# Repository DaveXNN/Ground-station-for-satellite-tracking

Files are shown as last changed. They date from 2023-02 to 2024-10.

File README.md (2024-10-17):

# Ground station for satellite tracking
This repository contains a description of the project Ground station for satellite tracking. The goal of this project was to build a ground satellite station that is able to receive signals from satellites operating at VHF (Very High Frequency) and UHF (Ultra High Frequency). The ground station constists of rotator, antennas, polarization switcher, receiver and station computer (laptop). Each part is describet in separate chapter.

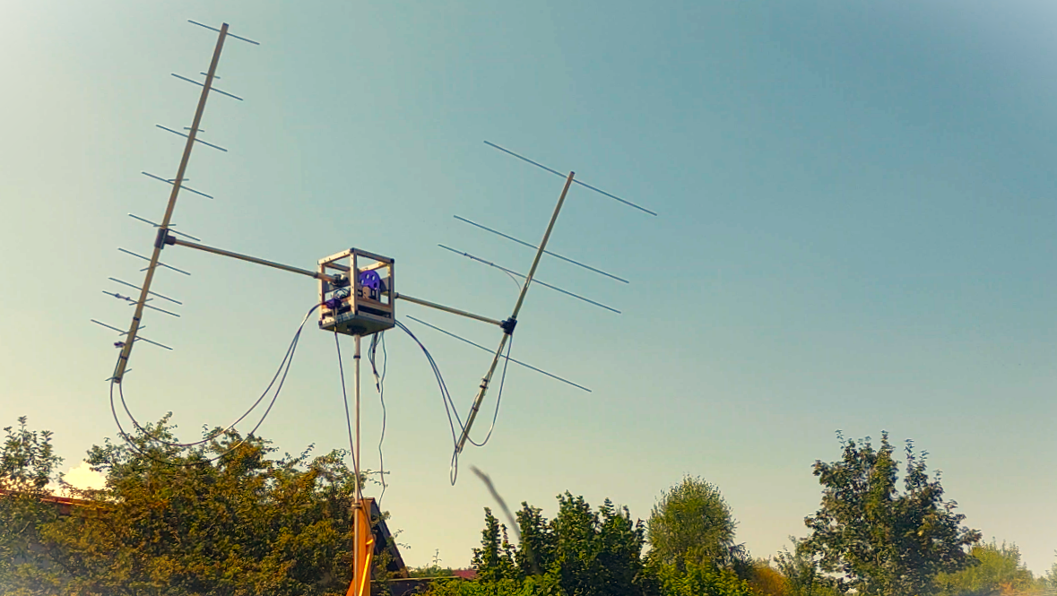
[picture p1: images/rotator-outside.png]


## Rotator
Unfortunately, a lot of these satellites are situated on the LEO (Low Earth Orbit), in other words below the altitude of 2 000 km. It means that the satellite changes its position very quickly and it's very uncomfortable to change antennas' direction manually, because it may cause a loss of the satellite signal. A rotator is a good solution of this problem, because this device moves the antennas automatically with very high precision.

### Design
Of course there are many proffesional rotators available to buy in the internet e.g. Yaesu, but i decided to build a similar rotator by myself, because it's cheaper option and I really wanted to get into this field of problems. I've got an inspiration from [SatNOGS Rotator v3](https://wiki.satnogs.org/SatNOGS_Rotator_v3).

The rotator frame is made from aluminium and wood and has dimensions of 240x240x305 mm. There are also 4 bearings installed, 2 to hold azimuth rod and 2 to hold elevation rod. It's also designed to mantle and dismantle easily, so each of the rods can be installed or removed quickly. Spur gears are used to make the rods to move. They are available with all 3D-printed parts in [this repository](/stl-files/rotator).

### Electronic components

The device is supplied by 45 W laptop charger providing 20 V voltage. This voltage is used to supply stepper motors, but it's also reduced into 5 V using step-down voltage regulator to supply control unit and polarization switchers. The control unit of the rotator is computer [Raspberry Pi 4](https://www.raspberrypi.com/products/raspberry-pi-4-model-b/) with its digital GPIO pins. Raspberry Pi controls two stepper motor drivers TB6600 and two polarization switchers described in chapter 3. The device is designed to require as few cables as possible so the communication between the rotator and station computer runs through WiFi.

Here is a list of electronic components:

| Name  | Quantity | Link |
| :--- | :---: | :---: |
| Raspberry Pi 4B  | 1  | https://www.raspberrypi.com/products/raspberry-pi-4-model-b/ |
| Step-Down Voltage Regulator LM2596 | 1 | https://www.laskakit.cz/step-down-menic-s-lm2596/ |
| Stepper motor NEMA23  | 2 | https://www.laskakit.cz/krokovy-motor-nema-23-57hs5630a4d8-1-1nm/ |
| Driver TB6600  | 2 | https://www.laskakit.cz/driver-tb6600--tb67s109aftg--pro-krokove-motory-3a-47v/ |
| Laptop charger 45 W | 1  |  |

#### Raspberry Pi 4B
The next picture depicts Raspberry Pi 4B pinout:

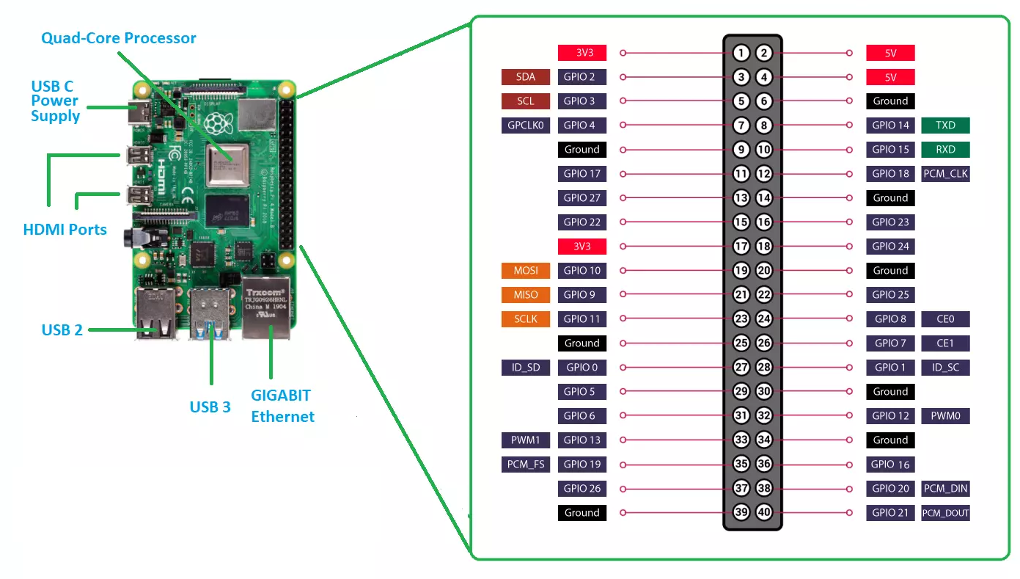
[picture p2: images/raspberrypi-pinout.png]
Raspberry Pi 4 pinout (www.theengineeringprojects.com)


In the next table you can see Raspberry Pi digital pins and their usage:

| Name | Pin number | GPIO code | Connected device | Description |
| :--- | :---: | :---: | :---: | :---: |
| VCC | 17 | 3V3 | Azimuth/elevation stepper motor driver | provides 3.3 V for controling drivers |
| az.ENA | 19 | GPIO10 | Azimuth stepper motor driver | enables stepper motor to move |
| az.DIR | 21 | GPIO9 | Azimuth stepper motor driver | sets rotation direction |
| az.PUL | 23 | GPIO11 | Azimuth stepper motor driver | used to do 1 single step |
| el.ENA | 11 | GPIO17 | Elevation stepper motor driver | enables stepper motor to move |
| el.DIR | 13 | GPIO27 | Elevation stepper motor driver | sets rotation direction |
| el.PUL | 15 | GPIO22 | Elevation stepper motor driver | used to do 1 single step |
| pol_sw.UHF_REL1 | 27 | GPIO0 | UHF polarization switcher | controls relay 1 |
| pol_sw.UHF_REL2 | 29 | GPIO5 | UHF polarization switcher | controls relay 2 |
| pol_sw.VHF_REL1 | 31 | GPIO6 | VHF polarization switcher | controls relay 1 |
| pol_sw.VHF_REL2 | 33 | GPIO13 | VHF polarization switcher | controls relay 2 |

#### Driver TB6600 (2x)
Driver TB6600 is supposed to control a stepper motor with a power supply 20 V. It has three inputs for controling stepper motor - ENA (enable), DIR (direction) and PUL (pulse) and for outputs A+, A-, B+, B-. Here is a list of all inputs and outputs of one stepper motor driver:

| Name | I/O | Connected device| Cable color | Voltage |
| :--- | :---: | :---: | :---: | :---: |
| ENA- | input | Raspberry Pi | green | 0/3.3 V |
| ENA+ | input | Raspberry Pi | red | 3.3 V |
| DIR- | input | Raspberry Pi | yellow | 0/3.3 V |
| DIR+ | input | Raspberry Pi | red | 3.3 V |
| PUL- | input | Raspberry Pi | orange | 0/3.3 V |
| PUL+ | input | Raspberry Pi | red | 3.3 V |
| B- | output | stepper motor | black | 0-20 V |
| B+ | output | stepper motor | green | 0-20 V |
| A- | output | stepper motor | blue | 0-20 V |
| A+ | output | stepper motor | red | 0-20 V |
| GND | input | Laptop charger | black | 0 V |
| VCC | input | Laptop charger | white | 20 V |

Each of the drivers also has six switches to set up peak current and microstep. Peak current is set to 0,7 V and microstep to level 4, it means that the position of the switches is: S1-ON, S2-OFF, S3-OFF, S4-ON, S5-ON, S6-ON.

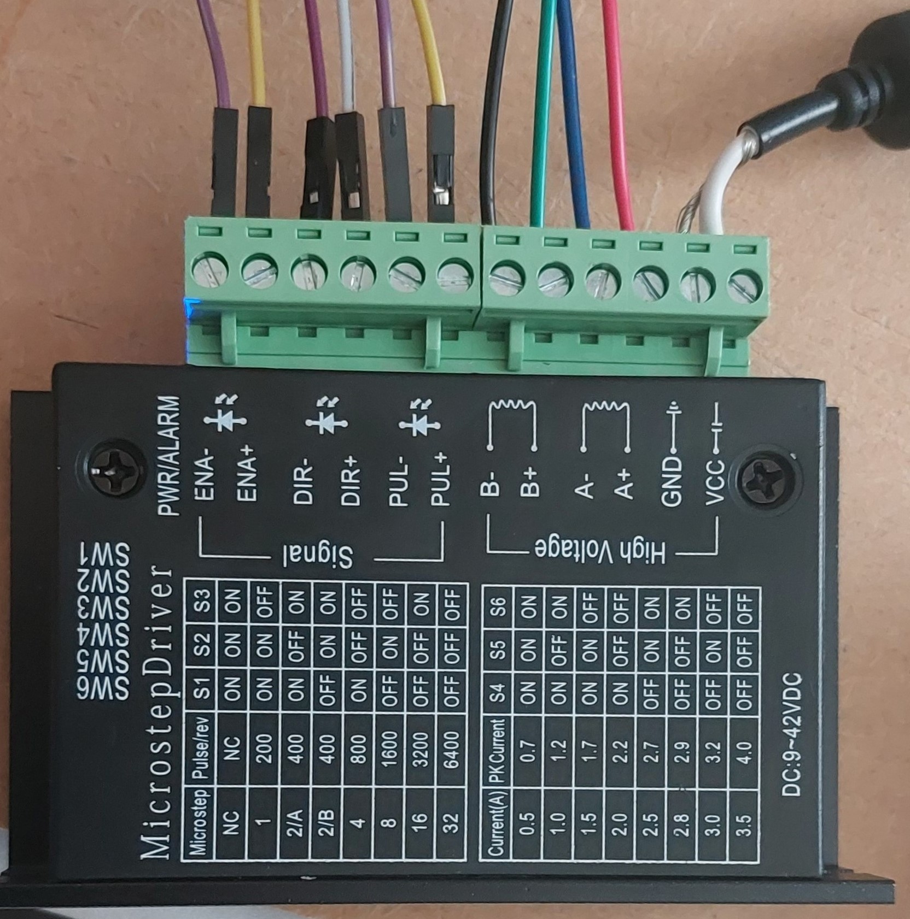
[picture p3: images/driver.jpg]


#### Stepper motor NEMA23 (2x)
NEMA23 is a high torque stepper motor with torque over 1,8 Nm and step angle 1,8°. It's connected with 4 wires (black, green, blue, red) to the driver. Stepper motors move the rotator via spur gears. In the next picture you can see spur gears for azimuth and elevation control.

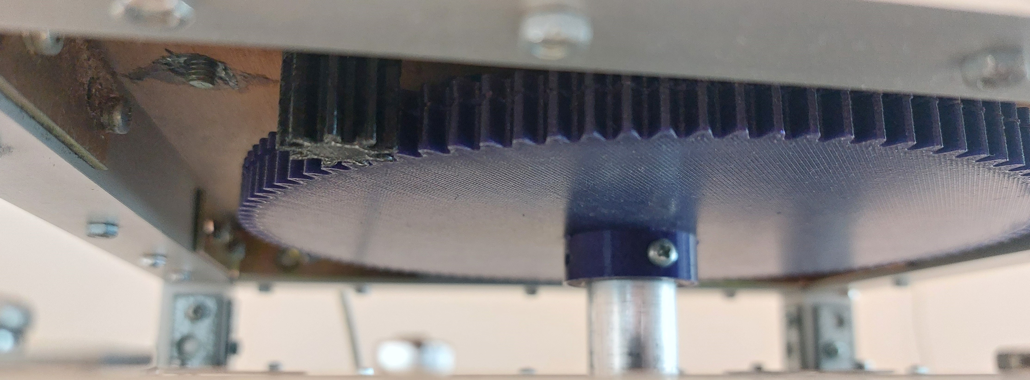
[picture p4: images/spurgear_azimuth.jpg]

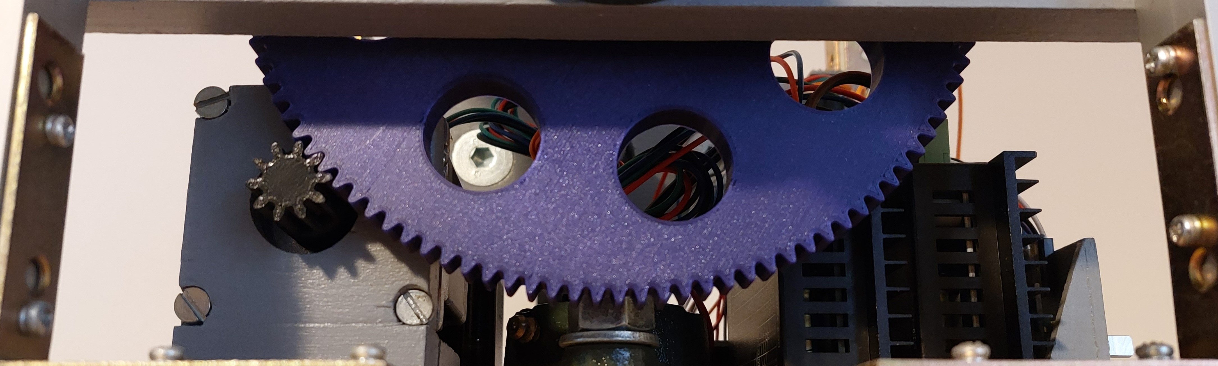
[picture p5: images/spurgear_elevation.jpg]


### Rotator software
Rotator receives commands via MQTT client and then moves stepper motors or changes antenna polarization. It's programmed in Python 3.9 and you can find the source code in [this repository](/source_code/rotator).

To install MQTT broker on Raspberry Pi I used a command ```sudo apt install -y mosquitto mosquitto-clients```

and to make Mosquitto auto start when the Raspberry Pi boots I used a command ```sudo systemctl enable mosquitto.service```.

[Rotator.py](/source_code/rotator/Rotator.py) is a main script that is run on boot. It initializes all modules and subscribes topics used to control rotator. There is also module [Stepper.py](/source_code/rotator/Stepper.py) to control stepper motors, module [PolarizationSwitcher.py](/source_code/rotator/PolarizationSwitcher.py) to control polarazation switchers and module [Publisher.py](/source_code/rotator/Publisher.py) to send rotator current azimuth and elevation back to station computer.

Here is a list of used Python packages:
* [RPi.GPIO](https://pypi.org/project/RPi.GPIO/) - controling digital pins
* [paho-mqtt](https://pypi.org/project/paho-mqtt/) - communicating with MQTT broker
* [threading](https://docs.python.org/3/library/threading.html) - running functions in parallel
* [time](https://docs.python.org/3/library/time.html) - time acces and conversions

For running script on boot of Raspberry Pi, I modified file ```/etc/rc.local``` by adding a line ```python3 /home/rotator/Rotator.py```, so the final file looks like this:
```
#!/bin/sh -e
#
# rc.local
#
# This script is executed at the end of each multiuser runlevel.
# Make sure that the script will "exit 0" on success or any other
# value on error.
#
# In order to enable or disable this script just change the execution
# bits.
#
# By default this script does nothing.

# Print the IP address
_IP=$(hostname -I) || true
if [ "$_IP" ]; then
  printf "My IP address is %s\n" "$_IP"
fi

python3 /home/rotator/Rotator.py &

exit 0
```

## Yagi antennas
The rotator has two arms equiped with cross-Yagi antennas for VHF and UHF. The VHF Yagi antenna is designed for frequency 145 MHz and the UHF Yagi antenna is designed for 435 MHz. The antennas are made from aluminium. For boom is made from 20 mm square rod and the elements are made from 6 mm circle rod.

The cross-Yagi antennas consist of two antennas on the same boom. The are rotated by 45 degrees and the shift between them is one fourth of the wavelangth ($\lambda/4$).

### VHF Yagi antenna (145 MHz)
The VHF Yagi antenna has 4 elements - reflector, radiator and 2 directors. The frequency 145 MHz corresponds with the wavelenth 2068 mm. All of the elements are described in the table below:

| Element | Length (mm) | Boom position (mm) | Gain (dBd) | Gain (dBi) |
| :--- | :---: | :---: | :---: | :---: |
| reflector | 1019.4 | 30 | - | - |
| radiator | 983.7 | 444 | - | - |
| director 1 | 946.1 | 598.6 | 4.8 | 6.9 |
| director 2 | 937.9 | 970.7 | 6.5 | 8.6 |

### UHF Yagi antenna (435 MHz)
The UHF Yagi antenna has 9 elements - reflector, radiator and 7 directors. The frequency 435 MHz corresponds with the wavelenth 689 mm. All of the elements are described in the table below:

| Element | Length (mm) | Boom position (mm) | Gain (dBd) | Gain (dBi) |
| :--- | :---: | :---: | :---: | :---: |
| reflector | 348.9 | 30 | - | - |
| radiator | 323.8 | 168 | - | - |
| director 1 | 313.5 | 219.5 | 4.8 | 6.9 |
| director 2 | 310.2 | 343.6 | 6.5 | 8.6 |
| director 3 | 307.1 | 491.7 | 7.8 | 9.9 |
| director 4 | 304.2 | 664.0 | 8.9 | 11.0 |
| director 5 | 301.6 | 857.0 | 9.8 | 11.9 |
| director 6 | 299.1 | 1063.8 | 10.5 | 12.7 |
| director 7 | 296.8 | 1280.9 | 11.2 | 13.3 |

## Polarization switchers
To change antenna polarization I built a polarization switcher. It is a device that is between antenna and receiver and can change the polarization between vertical, horizontal, right-handed circular polarization (RHCP) and left-handed circular polarization (LHCP). The device consists of two relays, that switch between two lenghts of coaxial cable, so they can shift the phase of comming signal from both antennas. VHF and UHF polarization switchers have different lenght of the cables because they are operating on different frequencies. The polarization switcher is inserted into a 3d-printed box and its STL model is located [here](/stl-files/polarization_switcher/polarization_switcher.stl).

## Receiver
Receiver [Airspy Mini](https://airspy.com/airspy-mini/) is used here.

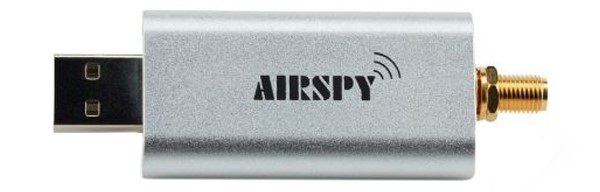
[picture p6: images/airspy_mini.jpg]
Airspy Mini


## Station computer software
Station computer (laptop) has a program called Satellite Tracking Software developed in Python 3.10. Source code is available [here](/source_code/station_computer). The program has a graphical user interface (GUI) and is used for predicting satellite visibility and controlling rotator. The program configuration is in a json file [configuration.json](/source_code/station_computer/configuration.json).

Within starting the program, the latest Two-line element (TLE) data are downloaded from [CelesTrak](https://celestrak.org/NORAD/elements/gp.php?GROUP=ACTIVE&FORMAT=tle). The data are updated every 2 hours, because it is the same period as CelesTrak uses for publishing the newest version of TLE. It is necessary to use the latest data for predicting satellite visibility, because when it's too old, the program may calculate the satellite position badly and the rotator won't be able to track the satellite correctly. Here is an example of TLE for the International Space Station or Czech satellite Planetum-1 from 31/8/2024:

```
ISS (ZARYA)             
1 25544U 98067A   24243.69891984  .00053939  00000+0  97276-3 0  9991
2 25544  51.6407 306.1908 0011145 301.8729 210.3060 15.49164437470102

PLANETUM1               
1 52738U 22057G   24244.10463033  .00126959  00000+0  21033-2 0  9999
2 52738  97.5706  13.4568 0006175 242.8845 117.1778 15.51691004126148
```

A text file [tle_active.txt](/source_code/station_computer/tle_active.txt) contains TLE data of all active satellites on the Earth's orbit. The list of all these satellite is displayed in GUI on the left hand side in the listbox All satellites. Next to the All satellites listbox there is another listbox called Selected satellites, which shows all satellites selected for tracking using buttons Add to tracking and Remove from tracking. The default screen looks like this:

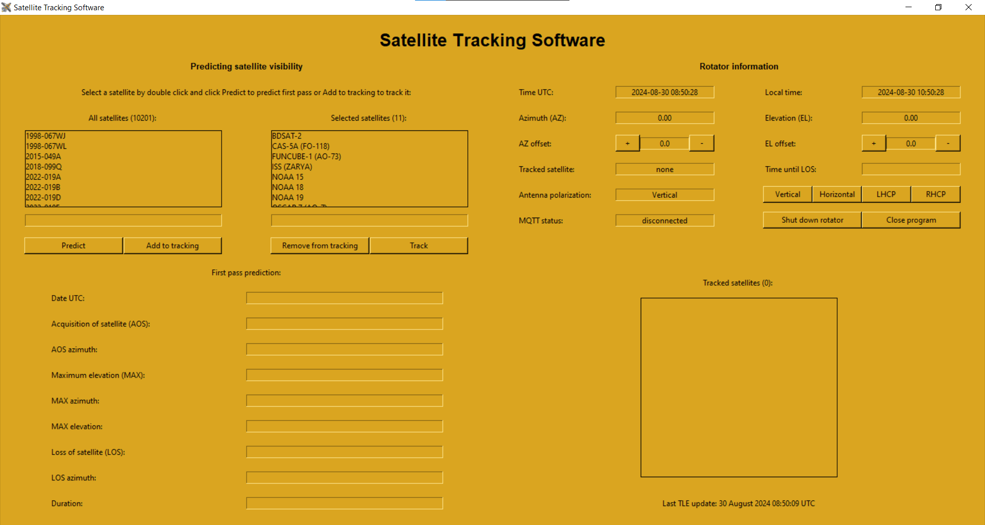
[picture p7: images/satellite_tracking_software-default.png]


You can select any of the satellites in All satellites listbox and predict its visibilityusing the Predict button. Information about the pass will be shown below in the table. Here is an example predict for the International Space Station (ISS):

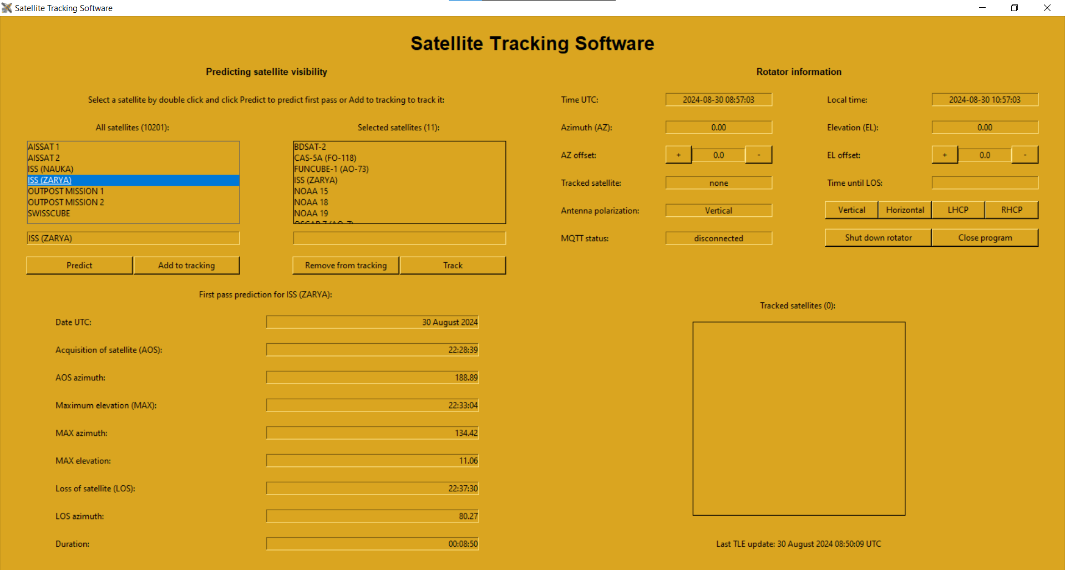
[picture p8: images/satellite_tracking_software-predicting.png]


The pass prediction consists of:
* Aquistition of the satellite (AOS) - time of the beginning of a pass
* AOS azimuth
* Maximum elevation (MAX) - time of the maximum elevation of a pass
* MAX azimuth
* MAX elevation
* Loss of the satellite (LOS) - time of the end of a pass
* LOS azimuth
* Duration - duration of the pass

On the left hand side, there is a rotator information section. When the rotator is turned of, its current azimuth and elevation is displayed here. While tracking, you can see name of tracked satellite and its time until LOS. You can also change antennas polarization by clicking on one of the buttons - Vertical, Horizontal, RHCP or LHCP. The current polarization is also shown here. Below the table, there is information about the next pass and listbox of satellite currently selected for tracking. On to bottom of the column there is a time of the latest TLE update. Here is the GUI while tracking satellite [Planetum-1](https://db.satnogs.org/satellite/CBUM-7092-9005-4302-8636).

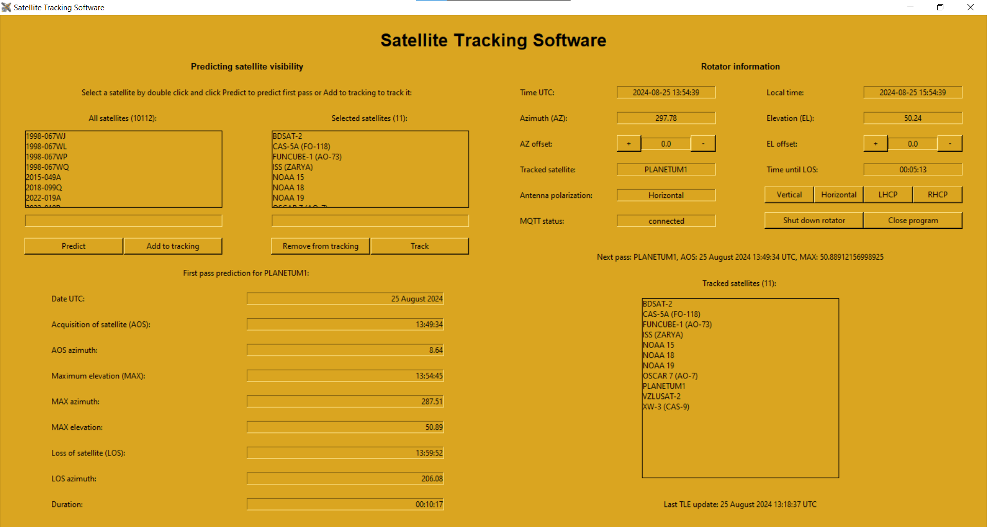
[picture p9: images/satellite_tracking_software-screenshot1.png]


Here is a list of used Python packages:
* [beyond](https://pypi.org/project/beyond/) - predicting satellite visibility
* [datetime](https://docs.python.org/3/library/datetime.html) - operations with date and time
* [json](https://docs.python.org/3/library/json.html) - coding and decoding json files
* [numpy](https://numpy.org/) - math operations
* [requests](https://pypi.org/project/requests/) - downloading TLE
* [socket](https://docs.python.org/3/library/socket.html) - MQTT connection errors
* [paho-mqtt](https://pypi.org/project/paho-mqtt/) - communicating with MQTT broker
* [threading](https://docs.python.org/3/library/threading.html) - running functions in parallel
* [tkinter](https://docs.python.org/3/library/tkinter.html) - creating GUI
* [time](https://docs.python.org/3/library/time.html) - time acces and conversions

### Functionality
In the beginning you select all satellites you want to track in the GUI. Then you click on the Predict button and the program calculates the first passes of selected satellites that is above minimum elevation set in [configuration.json](/source_code/station_computer/configuration.json). When any of the selected satellites appears above the horizon, station computer sends AOS azimuth to the rotator and the rotator moves to that azimuth. Then the station computer begins to send azimuth and elevation changes of satellite position in time. When the tracking is finished, the rotator returns to its default position (AZ: 0, EL: 0) and waits for another passing selected satellite to track.

## Experience with satellite tracking
Many tests have been done to ensure that everything in the antenna system is working well. The

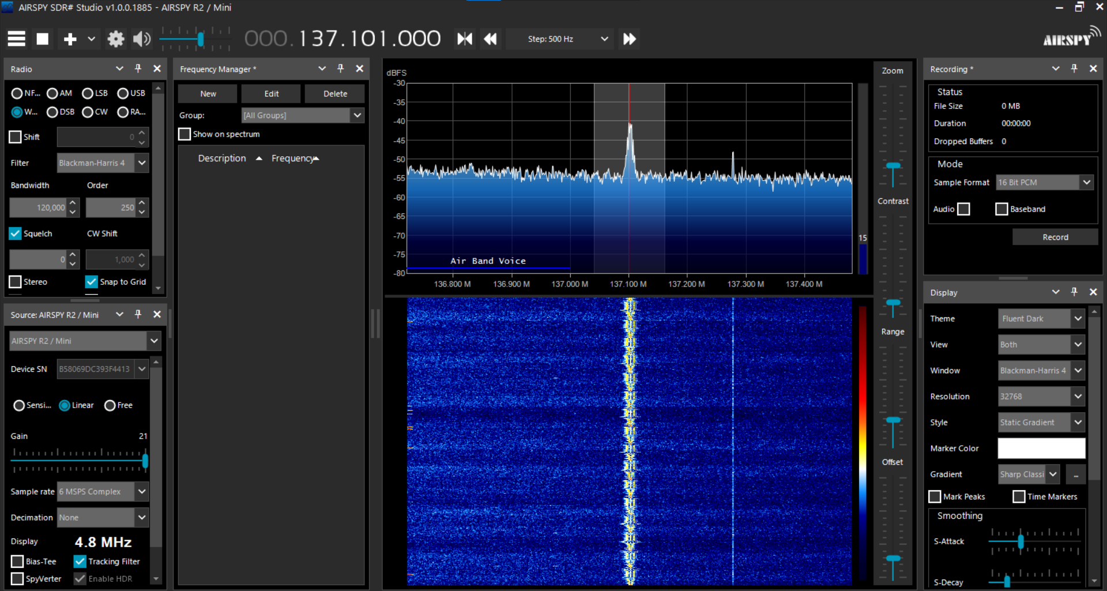
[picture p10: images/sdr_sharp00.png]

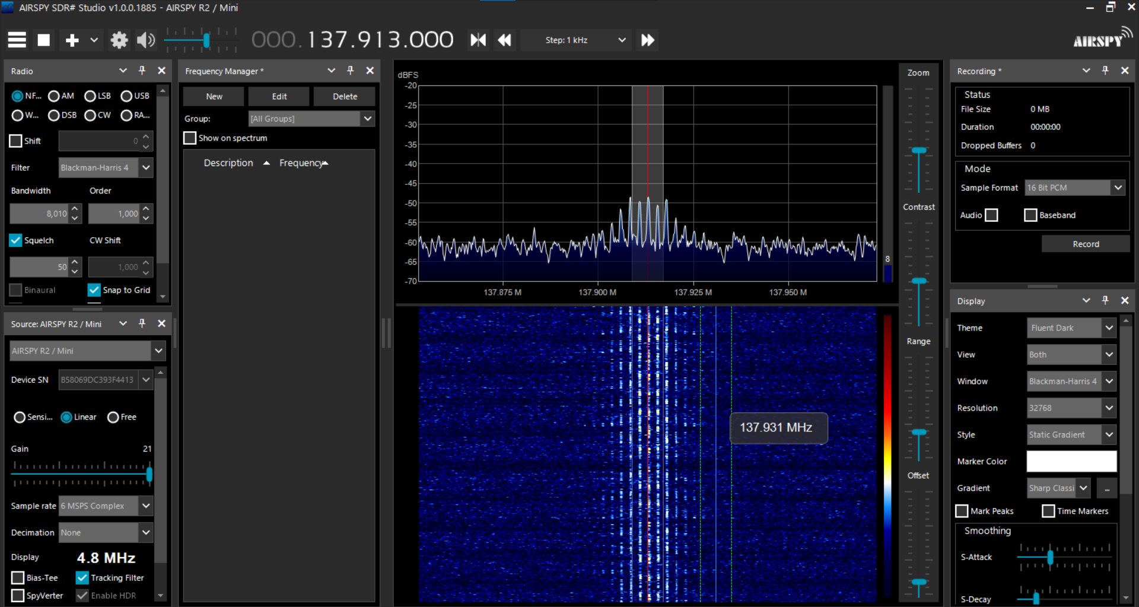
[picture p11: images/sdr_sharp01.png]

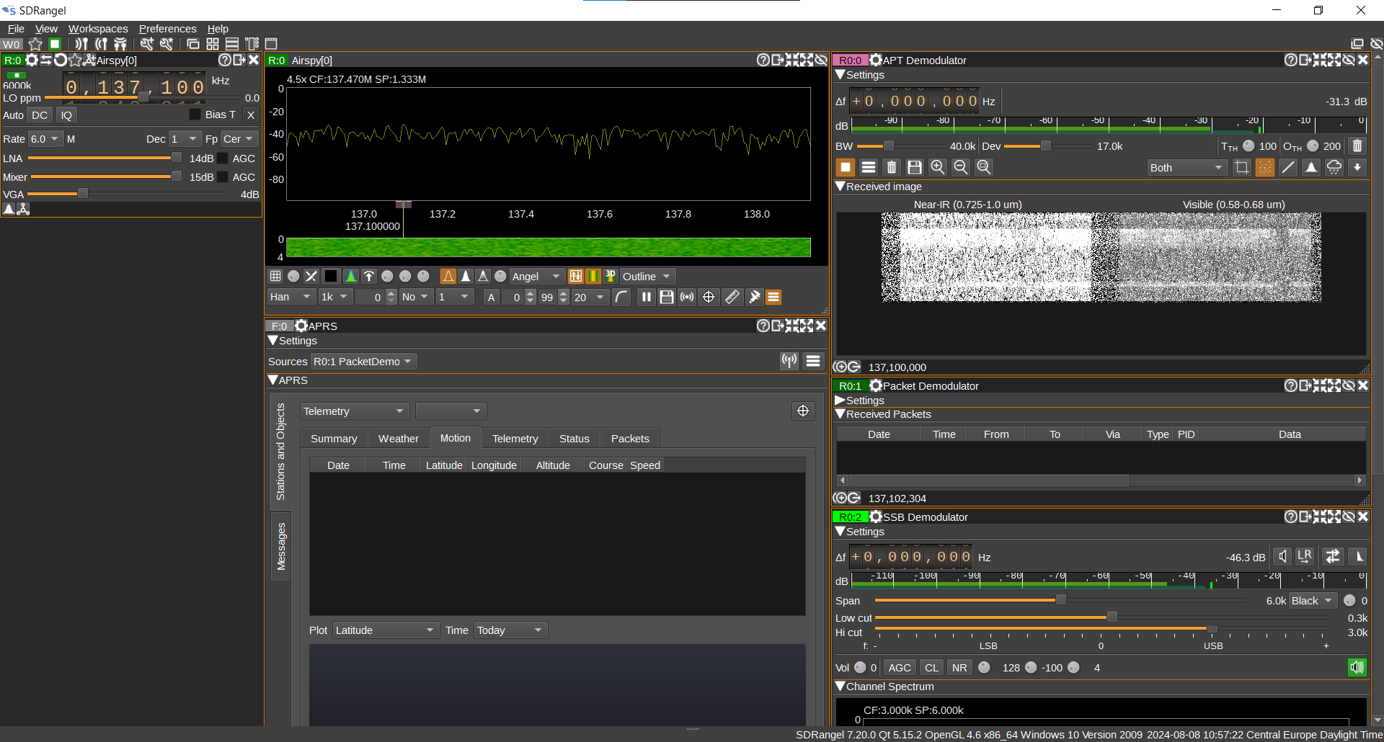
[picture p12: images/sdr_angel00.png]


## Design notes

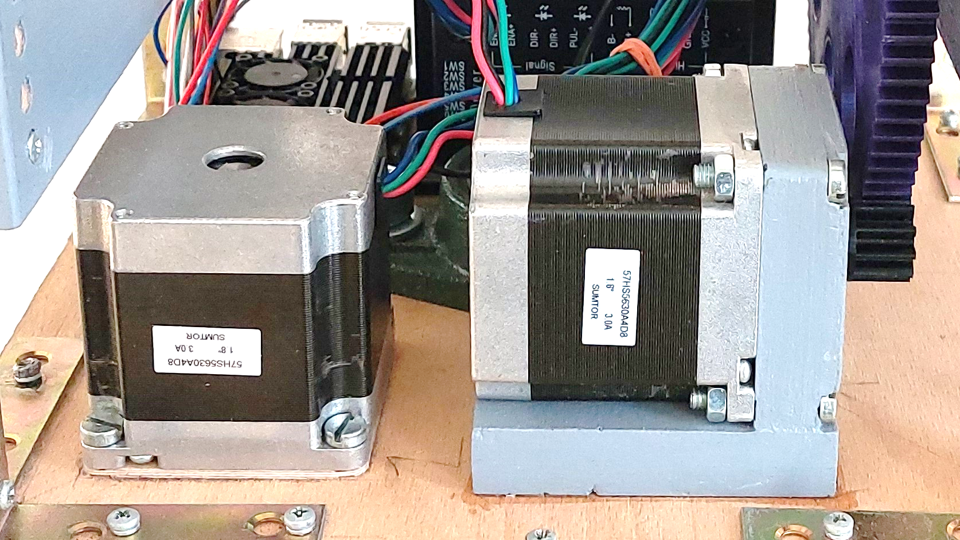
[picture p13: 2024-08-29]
images/stepper_motors.png

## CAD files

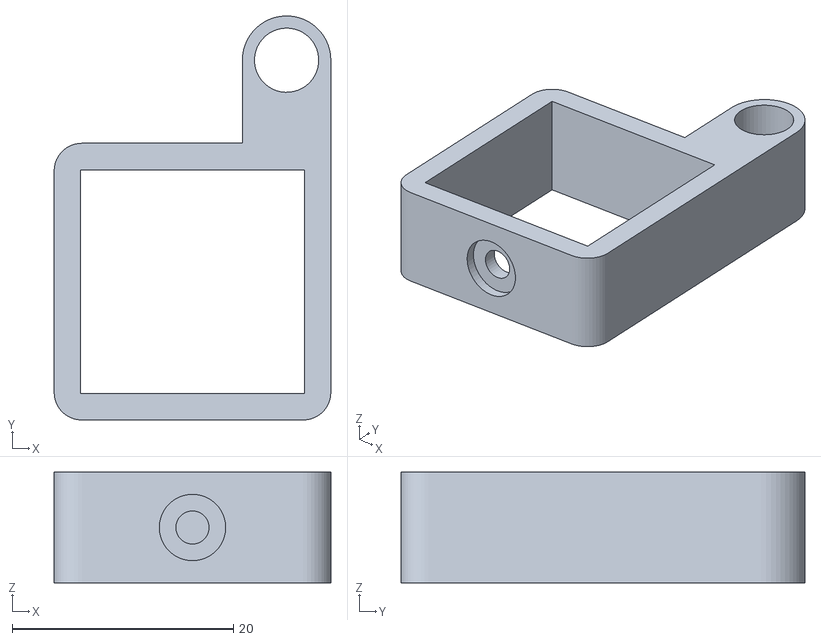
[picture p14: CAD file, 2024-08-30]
stl-files/antennas/coaxial_cabel_holder-1_cabel.stl
25.0 x 36.5 x 10.0

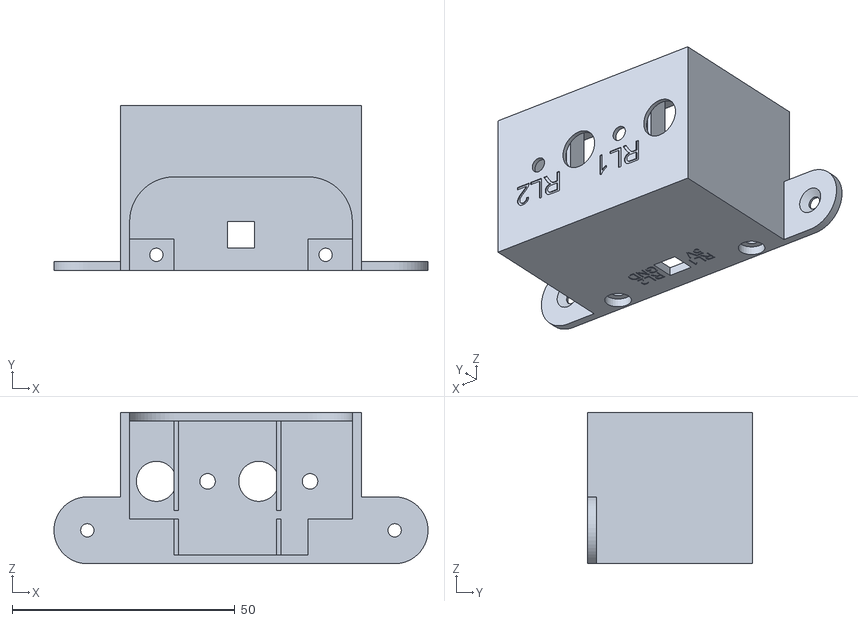
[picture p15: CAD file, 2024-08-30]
stl-files/polarization_switcher/polarization_switcher.stl
84.0 x 37.0 x 34.0

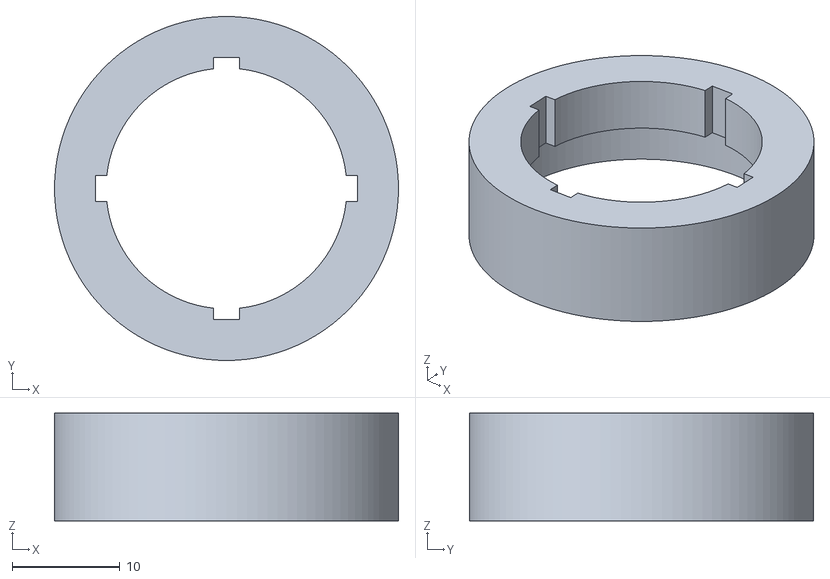
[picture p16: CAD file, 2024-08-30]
stl-files/rotator/rod_connector-outer.stl
32.0 x 32.0 x 10.0

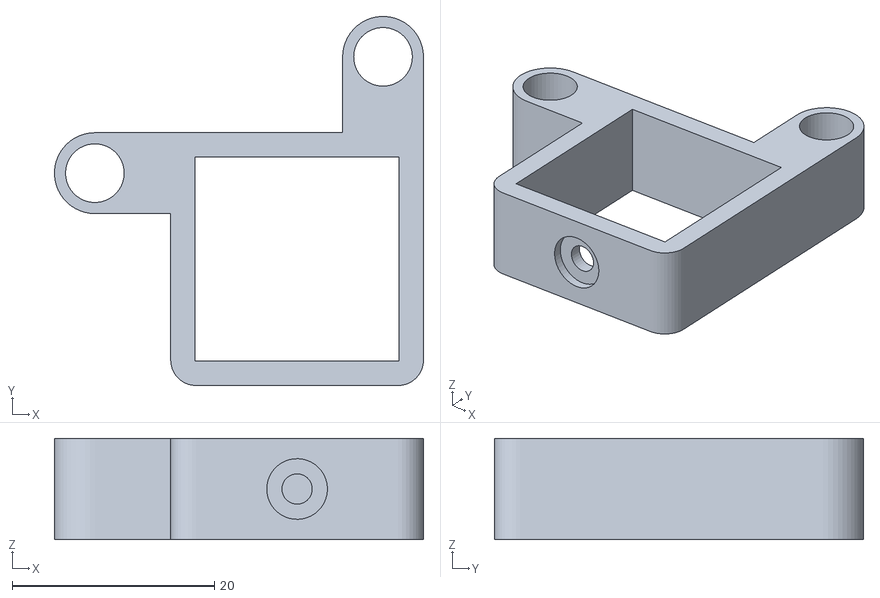
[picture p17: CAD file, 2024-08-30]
stl-files/antennas/coaxial_cabel_holder-2_cabels.stl
36.5 x 36.5 x 10.0

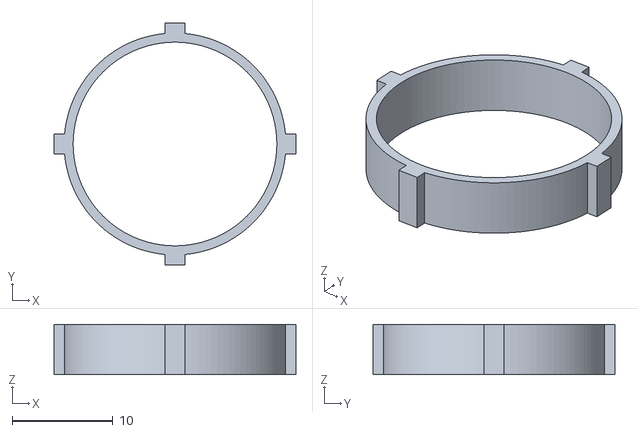
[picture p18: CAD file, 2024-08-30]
stl-files/rotator/rod_connector-inner.stl
24.0 x 24.0 x 5.00

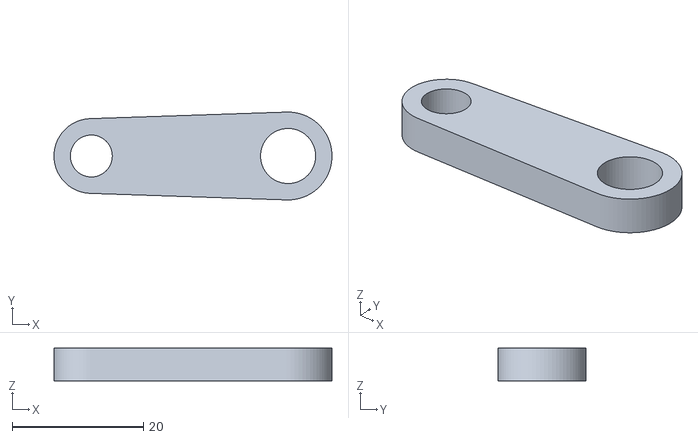
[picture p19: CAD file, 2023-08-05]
stl-files/antennas/gamma_match_holder-VHF.stl
42.4 x 13.4 x 5.00

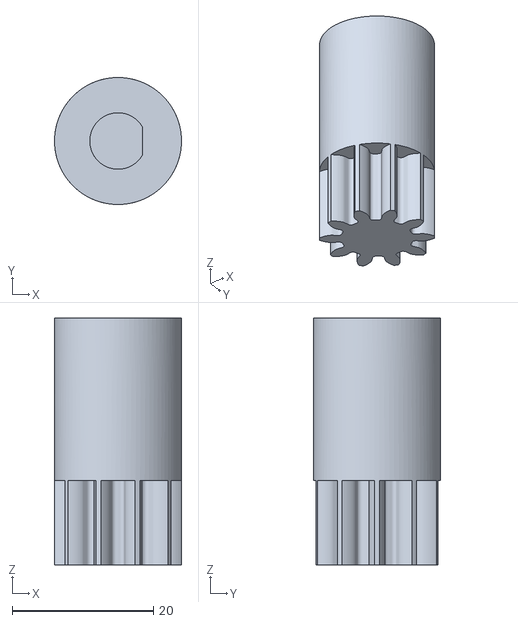
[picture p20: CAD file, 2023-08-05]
stl-files/rotator/spur_gear_10-azimuth.stl
18.0 x 18.0 x 35.0

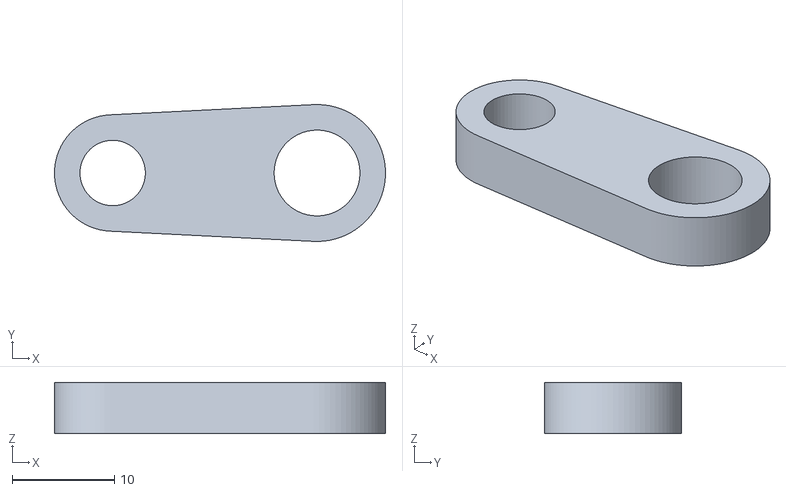
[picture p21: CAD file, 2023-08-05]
stl-files/antennas/gamma_match_holder-UHF.stl
32.4 x 13.4 x 5.00

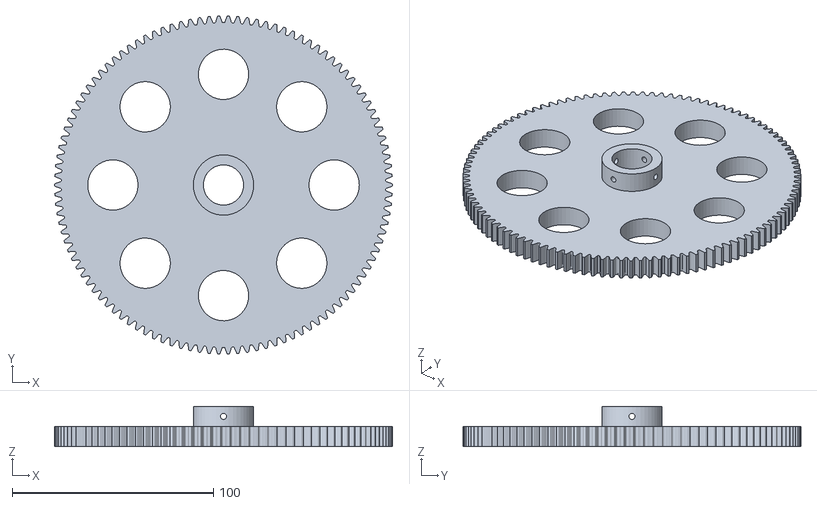
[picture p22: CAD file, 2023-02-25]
stl-files/rotator/spur_gear_110.stl
168.0 x 168.0 x 20.0

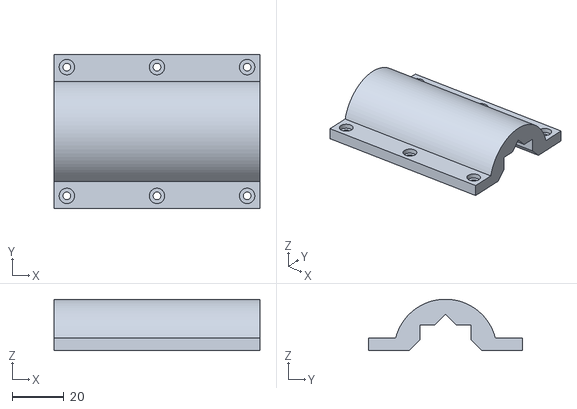
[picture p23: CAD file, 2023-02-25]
stl-files/rotator/antenna_holder-part2.stl
80.0 x 60.0 x 20.0

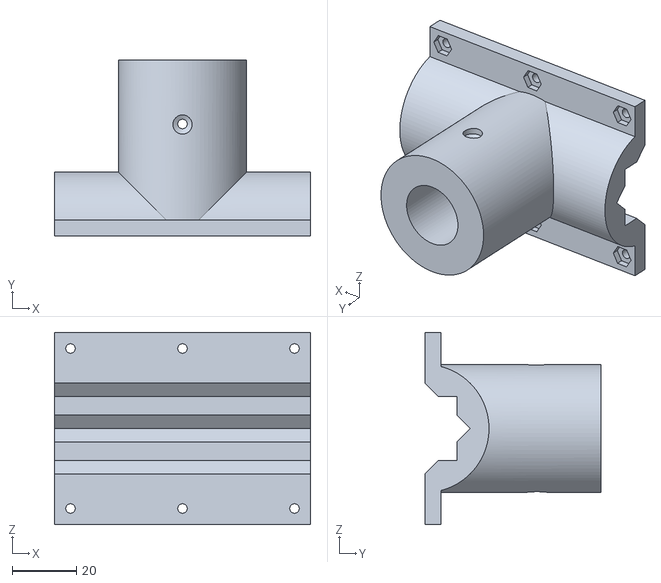
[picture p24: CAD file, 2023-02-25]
stl-files/rotator/antenna_holder-part1.stl
80.0 x 55.0 x 60.0

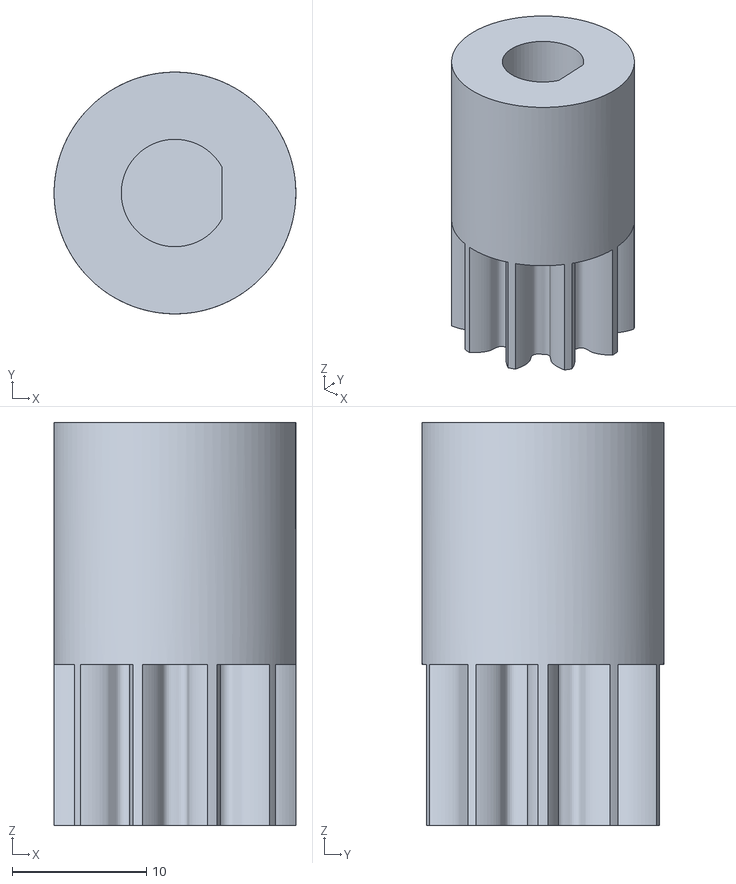
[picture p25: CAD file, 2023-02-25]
stl-files/rotator/spur_gear_10-elevation.stl
18.0 x 18.0 x 30.0

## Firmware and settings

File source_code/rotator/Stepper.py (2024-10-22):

###########################################################################################################################
#                                                                                                                         #
#    Author:         D. Nenicka                                                                                           #
#    Created:        3. 11. 2023                                                                                          #
#    Modified:       25. 8. 2024                                                                                          #
#    Description:    Module for stepper motor control                                                                     #
#                                                                                                                         #
###########################################################################################################################


import RPi.GPIO as GPIO                        # module for GPIO control

from threading import Timer                    # module for running multiple tasks in the same time
from time import sleep                         # module with sleep() function


class Stepper:
    def __init__(self, ena_gpio, dir_gpio, pul_gpio, e1, microstep, ratio, azimuth_mode=False):
        self.ena = ena_gpio                    # number of ENA pin
        self.dir = dir_gpio                    # number of DIR pin
        self.pul = pul_gpio                    # number of PUL pin
        GPIO.setup(self.ena, GPIO.OUT)         # set ENA as output
        GPIO.setup(self.dir, GPIO.OUT)         # set DIR as output
        GPIO.setup(self.pul, GPIO.OUT)         # set PUL as output
        self.a1 = e1 / (microstep * ratio)     # elementary angle (angle of 1 step)
        self.direction = 0                     # direction
        self.position = 0                      # position
        self.remain = 0                        # remaining angle
        self.offset = 0                        # offset
        self.i = 0                             # time increment
        self.i2 = 0                            # time increment of the first step
        self.sd = 0.00001                      # duration of 1 step
        self.dbs = 0.001                       # min. delay between 2 steps
        self.finished = True                   # status: False -> moving, True -> finished moving
        self.azimuth_mode = azimuth_mode       # mode
        self.enable_motor()                    # enable stepper motor
        self.set_positive_direction()          # set positive direction

    def enable_motor(self):                    # enable stepper motor
        GPIO.output(self.ena, GPIO.HIGH)
        GPIO.output(self.pul, GPIO.HIGH)

    def disable_motor(self):                   # disable stepper motor
        GPIO.output(self.ena, GPIO.LOW)
        GPIO.output(self.pul, GPIO.HIGH)

    def set_positive_direction(self):          # set positive direction
        GPIO.output(self.dir, GPIO.HIGH)

    def set_negative_direction(self):          # set negative direction
        GPIO.output(self.dir, GPIO.LOW)

    def step(self):                            # do 1 step
        GPIO.output(self.pul, GPIO.LOW)
        sleep(self.sd)
        GPIO.output(self.pul, GPIO.HIGH)

    def increase(self):                        # increase direction and position by 1 elementary angle
        self.direction += self.a1
        self.position += self.a1
        self.remain -= self.a1
        if self.azimuth_mode:
            if self.direction >= 360:
                self.direction -= 360

    def decrease(self):                        # decrease direction and position by 1 elementary angle
        self.direction -= self.a1
        self.position -= self.a1
        self.remain += self.a1
        if self.azimuth_mode:
            if self.direction <= 0:
                self.direction += 360

    def wait_until_finished(self):             # wait until another AZ process is finished
        while not self.finished:
            pass
        self.finished = False

    def set_speed(self, duration, angle):      # set speed (parameters: duration, angle)
        self.wait_until_finished()
        self.remain += angle
        self.i = (self.a1 * duration) / abs(self.remain)
        self.i2 = self.i / 2
        if self.remain >= self.a1:
            self.set_positive_direction()
            Timer(self.i2, self.step_forward).start()
        elif self.remain <= -self.a1:
            self.set_negative_direction()
            Timer(self.i2, self.step_backward).start()
        else:
            self.finished = True

    def step_forward(self):                    # 1 step in positive direction (usage: set_speed())
        self.step()
        self.increase()
        if self.remain >= self.a1:
            Timer(self.i, self.step_forward).start()
        else:
            self.finished = True

    def step_backward(self):                   # 1 step in negative direction (usage: set_speed())
        self.step()
        self.decrease()
        if self.remain <= -self.a1:
            Timer(self.i, self.step_backward).start()
        else:
            self.finished = True

    def move_to_direction(self, direction):    # move to different direction (before tracking)
        self.wait_until_finished()
        self.remain = self.remain + direction - self.direction
        if self.remain > 180:
            self.remain -= 360
        if self.remain < -180:
            self.remain += 360
        if self.remain >= self.a1:
            self.set_positive_direction()
            Timer(self.dbs, self.step_forward2).start()
        elif self.remain <= -self.a1:
            self.set_negative_direction()
            Timer(self.dbs, self.step_backward2).start()
        else:
            self.finished = True

    def step_forward2(self):                   # 1 step in positive direction (usage: move_to_direction(), reset_position())
        self.step()
        self.increase()
        if self.remain >= self.a1:
            Timer(self.dbs, self.step_forward2).start()
        else:
            self.finished = True

    def step_backward2(self):                  # 1 step in negative direction (usage: move_to_direction(), reset_position())
        self.step()
        self.decrease()
        if self.remain <= -self.a1:
            Timer(self.dbs, self.step_backward2).start()
        else:
            self.finished = True

    def reset_position(self):                  # reset position to zero
        self.wait_until_finished()
        self.remain -= self.position
        if self.remain >= self.a1:
            self.set_positive_direction()
            Timer(self.dbs, self.step_forward2).start()
        elif self.remain <= -self.a1:
            self.set_negative_direction()
            Timer(self.dbs, self.step_backward2).start()
        else:
            self.finished = True
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

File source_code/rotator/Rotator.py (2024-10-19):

###########################################################################################################################
#                                                                                                                         #
#    Author:         D. Nenicka                                                                                           #
#    Created:        3. 11. 2023                                                                                          #
#    Modified:       19. 10. 2024                                                                                         #
#    Description:    The main script, initializes all modules and subscribes topics from station computer via MQTT        #
#                                                                                                                         #
###########################################################################################################################


import os
import paho.mqtt.client as paho
import RPi.GPIO as GPIO

GPIO.setmode(GPIO.BCM)
GPIO.setwarnings(False)

from PolarizationSwitcher import PolarizationSwitcher
from Publisher import Publisher
from Stepper import Stepper


az_st = Stepper(10, 9, 11, 1.8, 4, 12.22222222, azimuth_mode=True)
el_st = Stepper(17, 27, 22, 1.8, 4, 11)
pol_sw = PolarizationSwitcher()
pub = Publisher(az_st, el_st) 


delta_t = 0
delta_az = 0
delta_el = 0
t_arrived = False
az_arrived = False
el_arrived = False
tracking = False


def on_connect(client, userdata, flags, rc):
    if rc == 0:
        print('Rotator connected to MQTT broker')
    else:
        print('Rotator not connected to MQTT broker', rc)


def on_message(client, userdata, message):
    global delta_t
    global delta_az
    global delta_el
    global t_arrived
    global az_arrived
    global el_arrived
    global tracking
    topic = str(message.topic)
    msg = str(message.payload.decode('utf-8'))
    if topic == 'action':
        if msg == 'start':
            tracking = True
        if msg == 'stop':
            az_st.reset_position()
            el_st.reset_position()
            tracking = False
        if msg == 'shutdown' and not tracking:
            az_st.disable_motor()
            az_st.disable_motor()
            os.system('sudo shutdown now')
    if topic == 'start_azimuth' and tracking:
        az_st.move_to_direction(float(msg))
        el_st.reset_position()
    if topic == 'delta_time' and tracking:
        t_arrived = True
        delta_t = float(msg)
    if topic == 'delta_azimuth' and tracking:
        az_arrived = True
        delta_az = float(msg)
    if topic == 'delta_elevation' and tracking:
        el_arrived = True
        delta_el = float(msg)
    if topic == 'polarization':
        pol_sw.set(msg)
    if topic == 'az_offset' and not tracking:
        az_st.set_offset(float(msg))
    if topic == 'el_offset' and not tracking:
        el_st.set_offset(float(msg))
    if t_arrived and az_arrived and el_arrived:
        az_st.set_speed(delta_t, delta_az)
        el_st.set_speed(delta_t, delta_el)
        t_arrived = False
        az_arrived = False
        el_arrived = False


client = paho.Client()
client.username_pw_set(<username>, password=<password>)
client.on_connect = on_connect
client.on_message = on_message
client.connect(<hostname>, port=<port>)
client.subscribe('action')
client.subscribe('start_azimuth')
client.subscribe('delta_time')
client.subscribe('delta_azimuth')
client.subscribe('delta_elevation')
client.subscribe('polarization')
client.subscribe('az_offset')
client.subscribe('el_offset')
client.loop_forever()
